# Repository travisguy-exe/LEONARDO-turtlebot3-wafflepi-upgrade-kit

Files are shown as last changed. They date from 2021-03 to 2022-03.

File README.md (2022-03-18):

# LEONARDO - Turtlebot3 (Waffle Pi) Upgrade Kit

**A 3D printable, open-source upgrade kit for the Turtlebot3 Waffle Pi from Robotis.**

 <span xmlns:dct="http://purl.org/dc/terms/" property="dct:title">LEONARDO - Turtlebot3 Waffle Pi Upgrade Kit</span> by <a xmlns:cc="http://creativecommons.org/ns#" href="https://github.com/travisguy-exe/LEONARDO-turtlebot3-wafflepi-upgrade-kit" property="cc:attributionName" rel="cc:attributionURL">Travis Guy</a> is licensed under a <a rel="license" href="http://creativecommons.org/licenses/by-nc-sa/4.0/">Creative Commons Attribution-NonCommercial-ShareAlike 4.0 International License</a>.

## **Kit Overview**

The Leonardo upgrade kit is intended to increase the overall modularity and usability of the Turtlebot3. This is a valuable upgrade for anyone looking to improve the physical user friendliness, durability and modularity of their Turtlebot3 unit. The following list outlines the key features of the Leonardo Kit.



####  **Kit Features:**

- **Enclosures:** Fully 3D printable enclosures for both the Turtlebot3's **Raspberry Pi** and **OpenCR** boards, with solid mounting points.
- **Solid LIDAR Mount:** A 3D printable solid mount for the LDS-01 LIDAR unit.
- **Improved User Experience** Careful consideration was made to relocate both the Raspberry Pi and OpenCR boards to make their ports more easily accessible. This combined with their solid mount points makes connecting peripherals and interfacing with the robot much easier than on the standard model.
- **Improved Modularity:** The Leonardo upgrade kit reimagines the construction of the Turtelbot3's waffle plate frame, allowing it to be segmented and customized without altering the original footprint or waffle plate pattern of the robot.  This feature allows access to the large amounts of free space within the Turtlebot3 frame so you can easily add your own modifications.

## **Repository Overview**

  This repository contains all of the files and instructions necessary to upgrade a standard Turtlebot3 Waffle Pi unit, as well as, the CAD documentation that one would require to add their own features to this upgrade kit. The following list provides detail on each of the sub-folders within this directory and where to locate relevant information within them.

**Repository Folders:**

- **3D Printing Files:** This folder contains all of the necessary **STL** files for printing the upgrade kit's parts.

- **CAD Files:** Contained within this folder are the **Fusion 360** and neutral **.step** solid models for the Leonardo Kit assembly and its sub-assemblies.

------

## **Project Log**

The Leonardo project is still under active development, which means features will be added to this repository as time goes on! Refer back to this log to see what is upcoming and what I have added!

### Work In Progress

- Custom URDF and mesh files of the Leonardo Kit variant for ROS.
- Youtube Assembly/Overview Video

### Completed Work

2021/03/26 - Project Inception

	- CAD Files - Leonardo v80 Master Assemblies
	- Assembly Documentation
	- STL Files/3D Printing Documentation

2022/03/18 - Youtube Assembly Video + CAD Model Update

```
- Assembly Video - Uploaded to Robotis OpenSourceTeam Youtube Channel
- Assembly Instuction - PDF Printable version of assembly documentation added to repository
- CAD Files - Leonardo Master Assembly updated to v83
- STL Files - Updated to Reflect V83 changes:
	 - USB relief added to OpenCR lower enclosure [02 - OpenCR Case (Lower) - (v118)]
	 - Update to RPi upper enclosure chamfer to improve printability [05 - RPi Case (Upper) - (v57)] 
```

------

## Assembly Video

https://youtu.be/VhC4pEQV8hI

## Bill of Materials

The following table outlines the items required to complete the Leonardo upgrade:

| Item/Description | Qty. | |
| :--- | :--: | :---: |
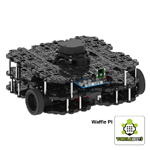
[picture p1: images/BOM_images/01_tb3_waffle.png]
| Turtlebot 3 Waffle Pi Kit |  1 |  |
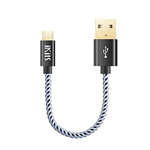
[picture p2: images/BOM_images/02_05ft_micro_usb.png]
| 0.5 ft. Micro USB Cable |  1 |  |
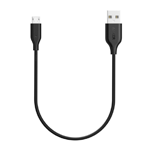
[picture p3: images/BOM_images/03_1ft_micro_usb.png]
| 1 ft. Micro USB Cable |  1 |   |
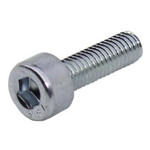
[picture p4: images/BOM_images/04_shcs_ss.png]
| **M3-0.5 x 8mm** - Socket Head Cap Screw |  16  |  |
| **M3-0.5 x 16mm** - Socket Head Cap Screw  |  16  |  |
| **M5-0.8 x 8mm** - Socket Head Cap Screw |  4 |  |
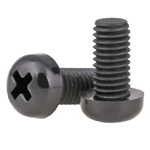
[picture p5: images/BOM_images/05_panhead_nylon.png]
| **M3-0.5 x 6mm** - Pan Head Screw (NYLON)  |  8 |   |
| **M3-0.5 x 12mm** - Pan Head Screw (NYLON) |  2 |   |

# **Assembly Instructions**

	This section outlines the assembly instructions for the Leonardo Upgrade Kit. These instructions assume that you have purchased all items in the **Bill of Materials** section and have 3D printed all relevant upgrade parts in accordance with the instructions laid out in the readme of the **3D Printing Files** folder.

------

### Step 1: TB3 First Layer Assembly

------

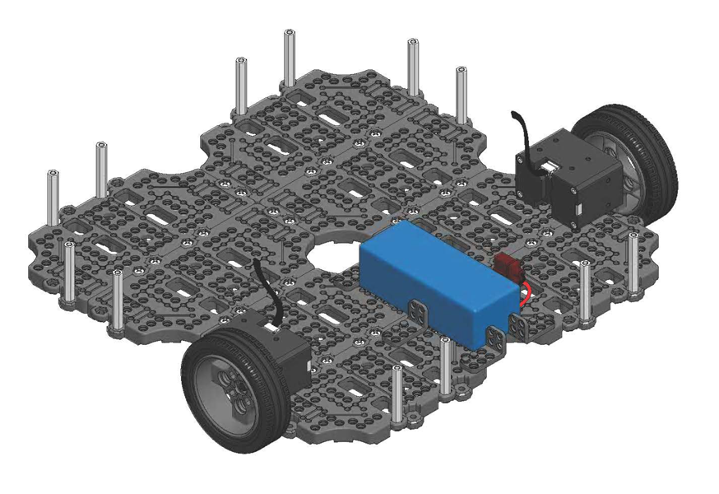
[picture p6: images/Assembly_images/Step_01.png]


The Leonardo upgrade kit uses the **"First Layer Assembly"** from the standard Turtlebot3 Waffle Pi. Specific instructions for assembling the **"First Layer Assembly"** can be found on **Pages 16-20** of the Robotis Turtlebot3 Waffle Pi Assembly Manual. Once assembled, the First Layer Assembly can be set aside until **Step 4**

**Robotis Assembly Manual (Direct Download):** https://www.robotis.com/service/download.php?no=750

------

### Step 2: TB3 Second Layer Assembly

------

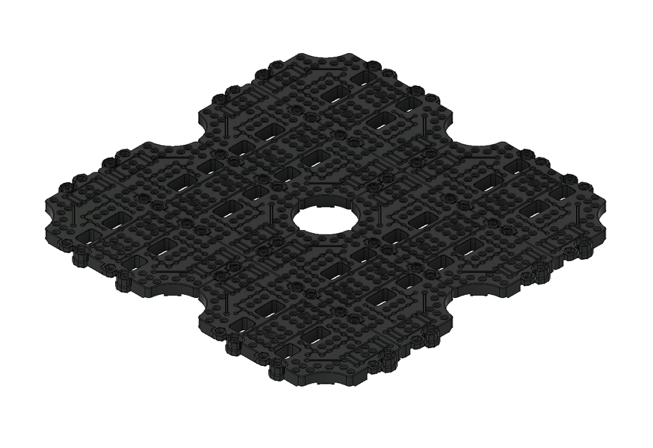
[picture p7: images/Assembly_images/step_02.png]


The Leonardo upgrade kit also uses the **"Second Layer Assembly"** from the standard Turtlebot3 Waffle Pi. Assembly instructions for the **"Second Layer Assembly"** can be found on **Pages 12-13** of the Robotis Turtlebot3 Waffle Pi Assembly Manual.  A fully assembled Second Layer is required before proceeding to **Step 3.**

------

### Step 3: Second Layer Drill & Tap Locations (Enclosure Mounting)

------

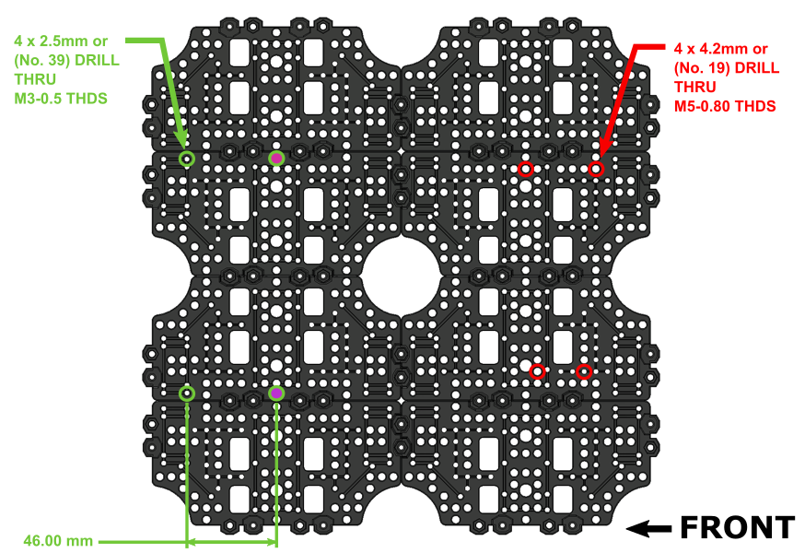
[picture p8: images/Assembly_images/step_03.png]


In order to attach the Raspberry Pi and OpenCR board enclosures, **6 pre-existing** holes must be modified and **2 new** holes must be added on the Second Layer Assembly.  

The **Step 3** image above indicates the relevant hole locations as well as their respective drill and tap sizes. The hole locations marked with **PINK** indicate where a new hole must be drilled. The location distances for the new holes are denoted on the image above, however, if one wishes to avoid measuring, the 3D printed lower case of the OpenCR board enclosure can be used as a template to transfer the hole locations to the waffle plate before drilling.

**NOTE:** Orientation of the second layer assembly matters from this step onwards. Be sure to follow the orientation indicators for each subsequent step.

------

### Step 4: Second/Third Layer Standoff Installation

------

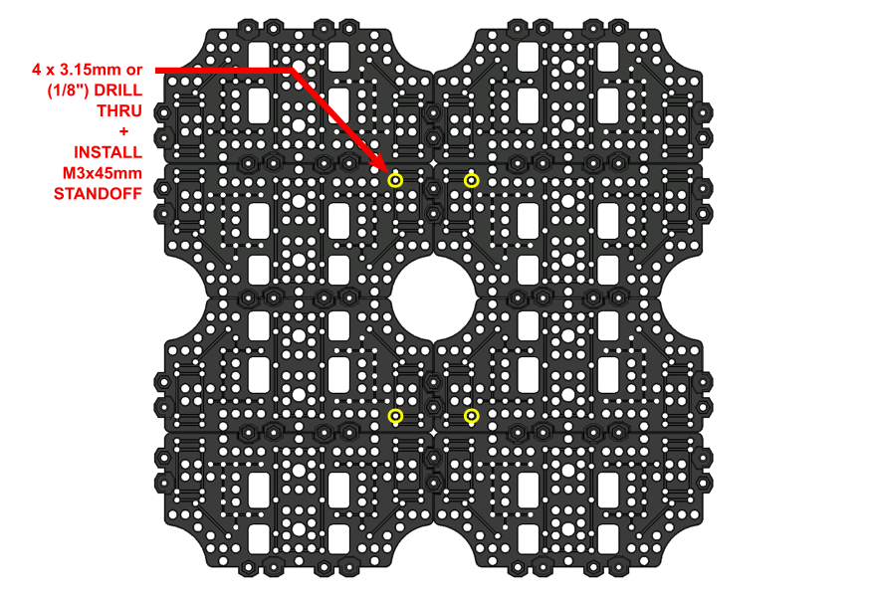
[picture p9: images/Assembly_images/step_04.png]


The third layer of the Leonardo upgrade kit is supported by **4 - M3x45mm Standoffs** attached to the second layer assembly. These standoffs are re-purposed hardware from the standard Turtlebot3 kit and can be obtained from such. **4 - M3x16mm** fasteners will be required to attach the standoffs.

The Step 4 image above indicates the correct installation location of each standoff, before installation the indicated holes must be  drilled out for an M3 free fit (3.15mm or 1/8" Drill).

**NOTE:** Ensure mounting screws for the standoffs are tightly secured and in the correct positions before proceeding. Once the second layer assembly is attached to the first, you will loose convenient access to the screw heads for these standoffs.

------

### Step 5: Second Layer Attachment + Cable Routing

------

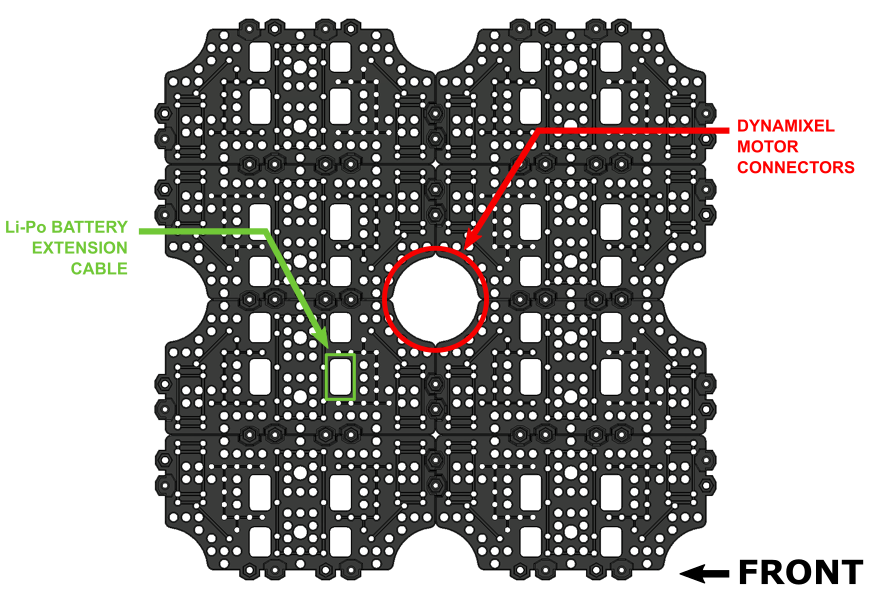
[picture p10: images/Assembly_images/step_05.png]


At this stage the **Second Layer Assembly** created in **Step 2** can be attached to the **First Layer Assembly** created in **Step 1**. However, before attachment, the **Dynamixel Motor Cables** and the **Li-Po Battery Extension Cable** from the first layer must be correctly routed through the bottom of the Second Layer Assembly. The **Step 4** image above shows the respective routing locations for the cables. 

A total of **12 - M3x8mm** screws will be required to attach the second layer to the first. Socket head cap screws can be used if you wish, or you can repurpose the Philips head hardware of the same size from the original Turtlebot3 kit. 

------

### Step 6: OpenCR + Raspberry Pi Installation 

------

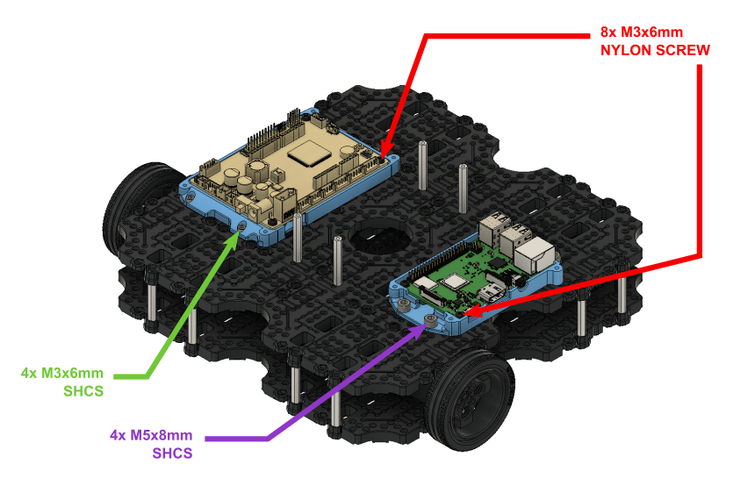
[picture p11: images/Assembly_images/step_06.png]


The **OpenCR** board and **Raspberry Pi**  can now be installed into their respective enclosure halves using **8 - M3x6mm Nylon Screws**. Once installed the enclosures can be attached to the **Second Layer Assembly** using the drilled and tapped holes created in **Step 2** of these instructions. The **Step 5** image above shows the required mounting hardware and respective installation locations.

**NOTE:** The mounting holes on the Raspberry Pi board may need to be enlarged for the M3 Nylon Screws if you have a brand new board. A 3.15mm or (1/8") drill bit will suffice for this process.

------

### Step 7: OpenCR Board Connections + Bluetooth Module Installation (BT-410)

------

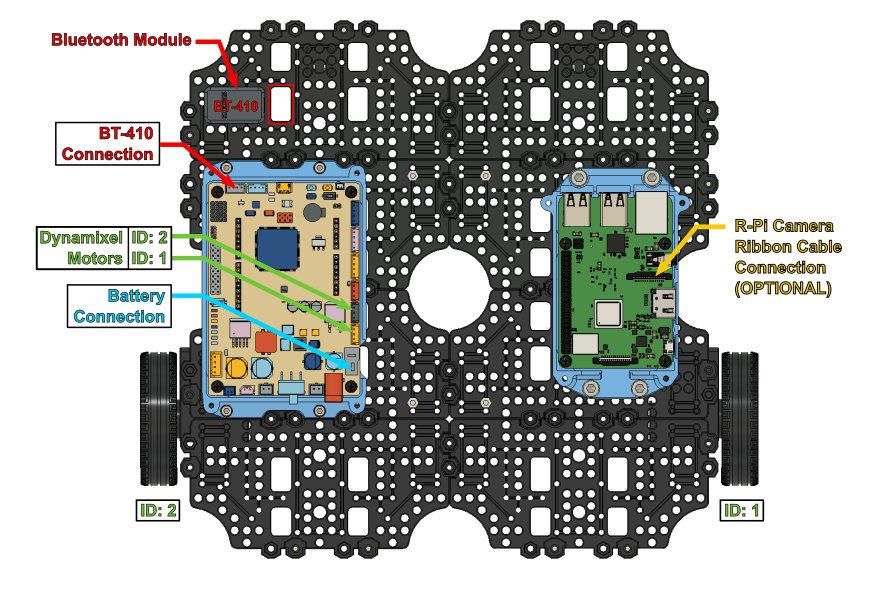
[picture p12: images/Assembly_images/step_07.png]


- [ ] Attach the **Dynamixel Motor** cables and **Li-Po Battery Extension** cable that were routed during **Step 5** to the OpenCR board. The connection points are indicated by the **Green** and **Blue** arrowed text in the image above. 

  **NOTE:** Ensure correct connection of the Dynamixel motors by following the motor ID legend in the **GREEN** arrowed text. The motor IDs are indicated below each wheel for quick reference.

- [ ] Once the motor and battery connections are made, attach the **BT-410 Bluetooth Module** to the second layer assembly. The **RED** arrowed text above indicates its installation location as well as connection point on the OpenCR board.

  **NOTE:** The opening highlighted by the **RED** rectangle can be used to neatly tuck away the excess cable from the Bluetooth module.

- [ ] **OPTIONAL:** If you wish to use the standard Raspberry Pi camera that comes with the Turtlebot3 kit, now is the easiest time to connect the camera's ribbon cable. The **ORANGE** arrowed text above indicates its connection point.

  **NOTE:** It is easy to connect the camera cable backwards, ensure that the camera ribbon cable is connected in the correct orientation (Contacts on the ribbon cable facing the contacts on the port.)

------

### Step 8: Enclosure Assembly + Raspberry Pi Power Connection

------

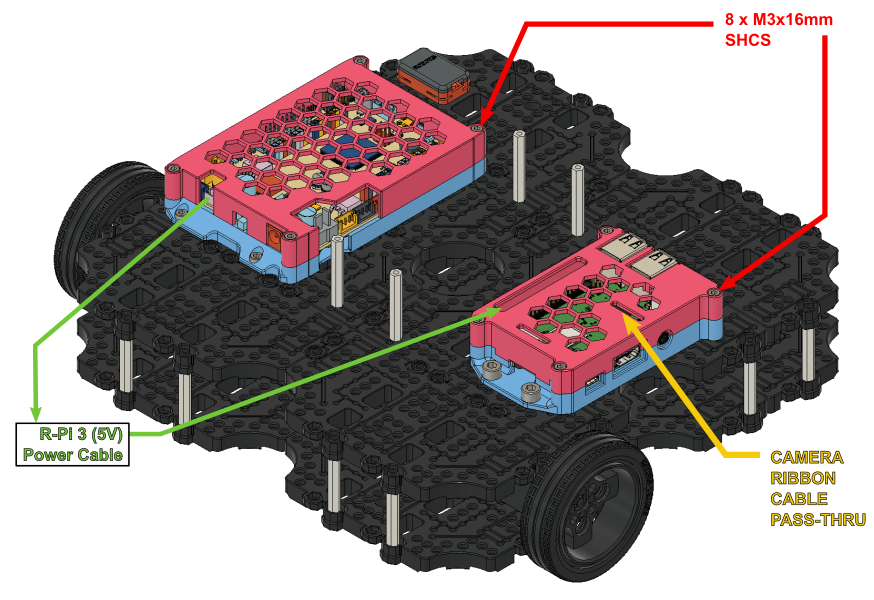
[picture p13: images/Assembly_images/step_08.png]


- [ ] The top halves of the enclosure cases can now be attached to the assembly. As indicated in the assembly image above, a total of **8 - M3x16mm** fasteners will be required. If you are using a R-Pi camera, be sure to route the ribbon cable through the pass through opening indicated above by the **YELLOW** arrowed text.

- [ ] Once the enclosure cases are securely installed the 5V power connection between the OpenCR board and the Raspberry Pi board can be made. This is done using the **Raspberry Pi 3 Power Cable** from the standard Turtlebot3 kit.  The **GREEN** arrowed text in the image above indicates the connection points.

  **NOTE:** When connecting the power cable to the Raspberry Pi it is important to connect to the correct GPIO pins. Ensure that the **Positive** lead connects to **Pin 4** and the **Negative** lead connects to **Pin 6**. 

  (Refer to **Page 23** of the Turtlebot3 Waffle Pi Assembly Manual for connection information.)

------

### Step 9:  Third Layer Assembly + Tap & Drill Instructions

------

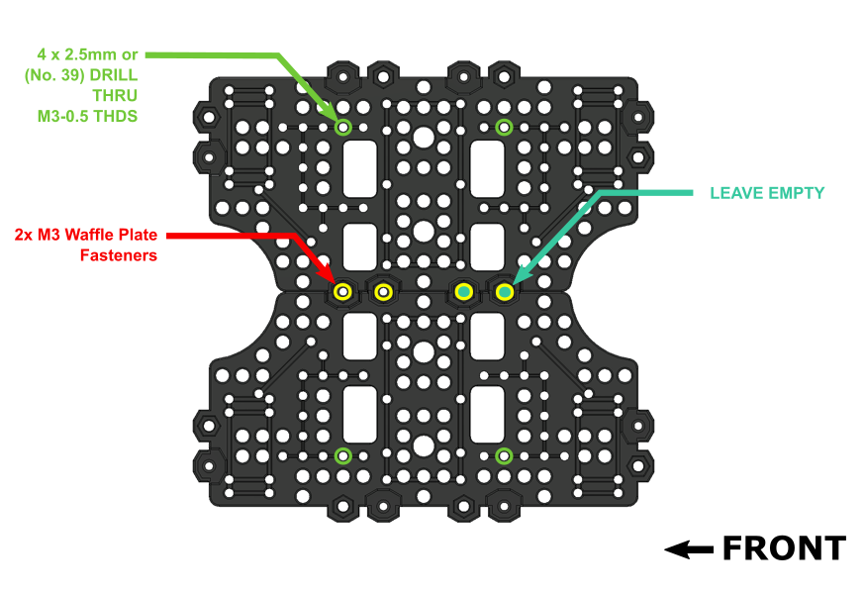
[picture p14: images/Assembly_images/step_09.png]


The third layer of the Leonardo upgrade requires only two waffle plates from the standard Turtlebot3 kit. The **Step 9** image above shows the manner in which the plates are connected and, indicates the fastener installation locations.

**NOTE:** It is important to leave the two M3 fastener locations indicated in the image above empty. These locations are used for attaching the USB2LDS driver board in the next step.

Once the waffle plates are assembled, and, before proceeding to the next step, a total of **4** pre-existing holes on the assembly must be modified. The **GREEN**  arrowed text in the **Step 9** image above indicates the relevant holes, as well, their respective drill and tap information.

------

### Step 10:  USB2LDS Module Installation

------

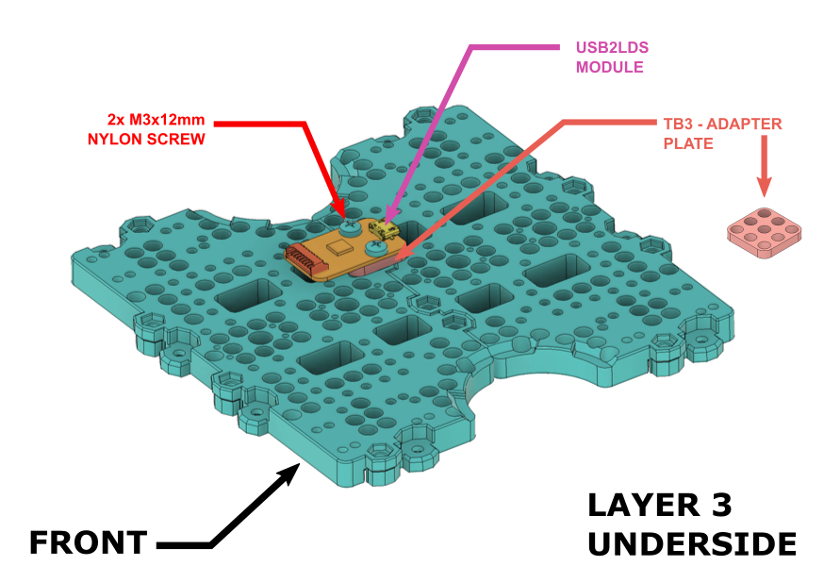
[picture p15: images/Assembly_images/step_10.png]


The USB2LDS module from the standard Turtlebot3 kit can now be installed on the underside of the the third layer assembly.  The module requires **2 - M3x12mm Nylon screws** that are fastened through the waffle plates in the fastener locations left empty in **Step 9**. As indicated in the image above the assembly also requires the **"Adapter Plate"** component from the standard Turtlebot3 kit, this component acts as a spacer for the module.

**NOTE:** The Nylon screws will protrude through the topside of the waffle plates. Use a pair of **flush-cut pliers** to trim the excess after the module has been tightly secured.

------

### Step 11:  LIDAR Mounting Bracket Installation

------

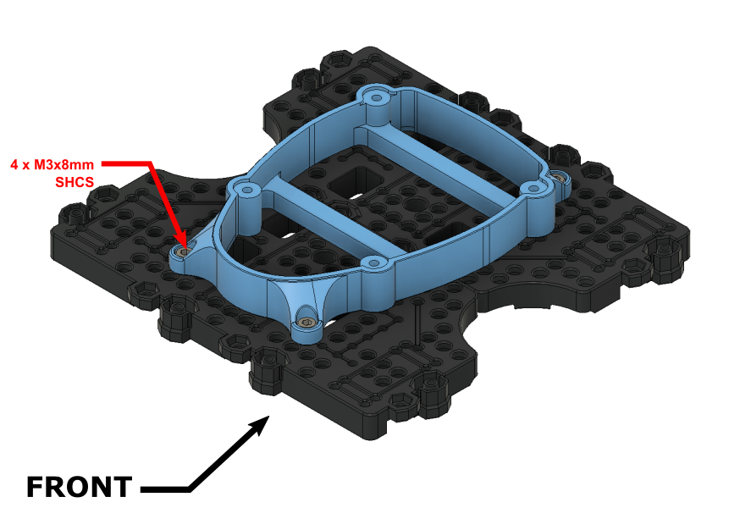
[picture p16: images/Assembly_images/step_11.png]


Turn the Layer 3 assembly back over and attach the LIDAR mount bracket to the top side using **4 - M3x8mm Socket Screws**.  The LIDAR bracket's mounting position corresponds with the 4 drilled and tapped holes made previously in **Step 9**.

------

### Step 12:  LIDAR Module Installation (LDS-01)

------

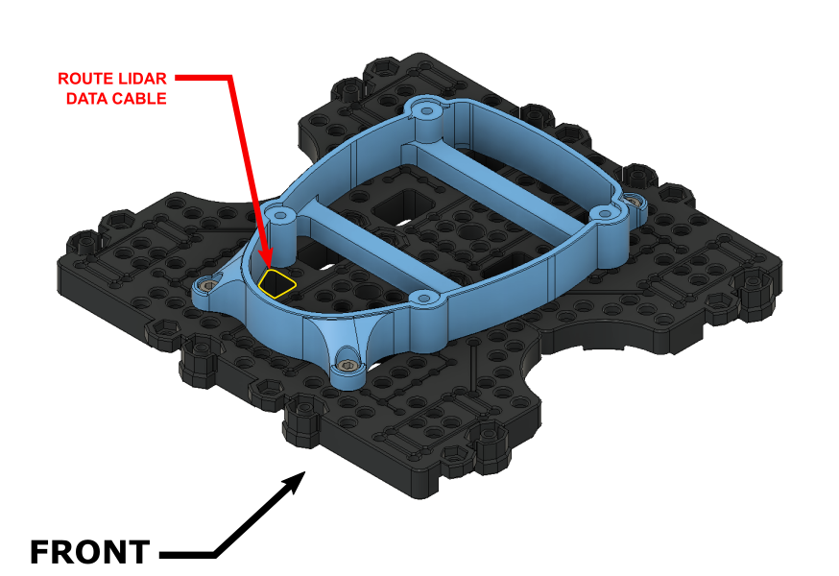
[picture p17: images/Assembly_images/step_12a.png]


------

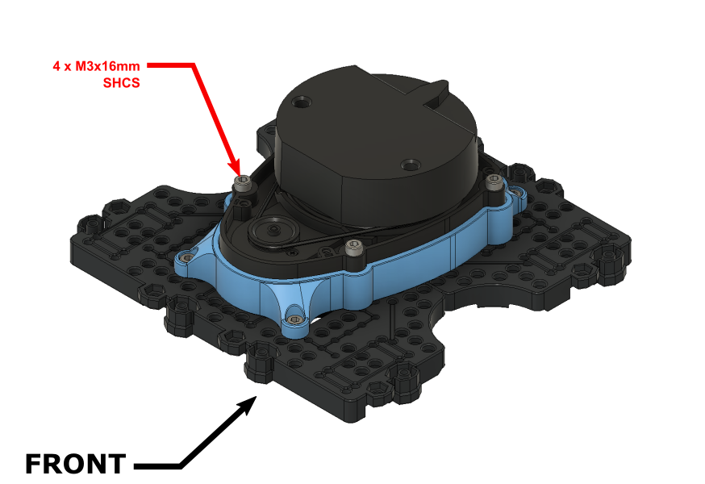
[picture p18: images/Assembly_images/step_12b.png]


See the **NOTE** below before proceeding. Attach the LDS-01 LIDAR unit from the standard Turltbot3 kit to the mounting bracket using **4 - M3x16mm Socket Screws**. Be sure to route the unit's data cable though the opening highlighted in **YELLOW** in the image above before fastening. Once fastened make sure to attach the LDS-01's data cable to the USB2LDS module on the underside of the layer.

**NOTE:** The LIDAR unit's mounting holes will have to be modified to accept M3 sized fasteners. Drill out the 4 indicated mounting holes using a 3.15mm or (1/8") drill bit.

------

### Step 13:  Third Layer Attachment

------

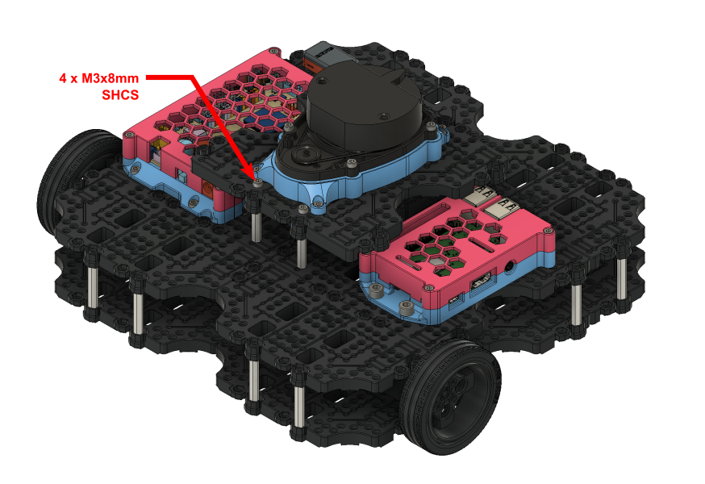
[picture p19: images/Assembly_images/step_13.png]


Attach the third layer assembly to the standoffs that were previously installed on the second layer assembly during **Step 4**. This will require **4 - M3x8mm Socket Screws**.

------

### Step 14:  Pi Camera Module Installation (Optional)

------

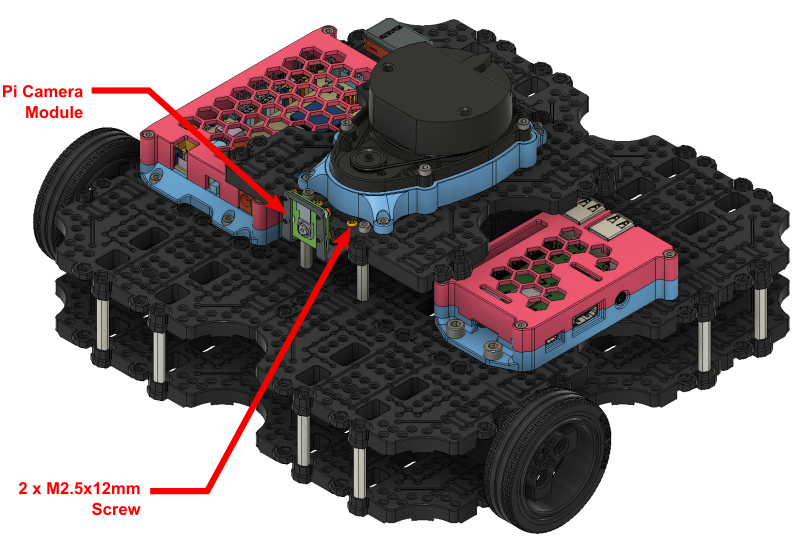
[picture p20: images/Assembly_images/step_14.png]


If you plan on using the standard Pi Camera module that comes with the Turltbot3 kit, it can now be easily attached to the **Third Layer Assembly ** using the standard M2.5x12mm mounting hardware that comes with it. 

**NOTE:** See page 30 of the Robotis Turtlebot3 Waffle Pi Assembly Manual for detailed instructions on assembling the Pi Camera module.

------

### Step 15: USB Connections and Cable Routing

------

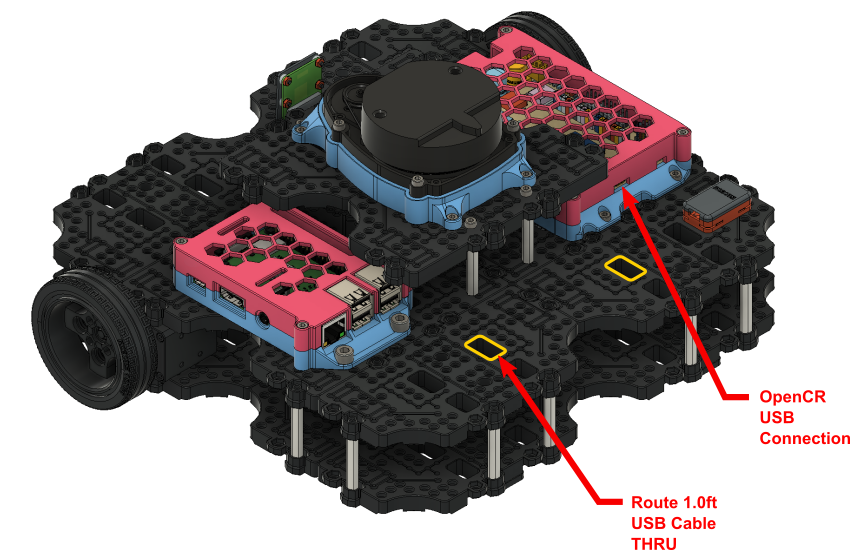
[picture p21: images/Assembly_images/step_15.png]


The final steps are to make the USB connections to both the USB2LDS module and the OpenCR board from the Raspberry Pi unit.

- [ ] Connect the 0.5ft micro USB cable from the Raspberry Pi unit to the USB2LDS module beneath the third layer assembly
- [ ] Connect the 1.0ft micro USB cable from the Raspberry Pi unit to the OpenCR board.

**NOTE:** The 1.0ft micro USB cable should be routed through the holes highlighted in **YELLOW** on the way towards the OpenCR board, this will keep the cable routing tidy and out of the way during use.

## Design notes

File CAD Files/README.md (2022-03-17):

# **LEONARDO - CAD FILES - (v83)**

This folder contains the master assembly file for the LEONARDO mod kit, it is available in 2 different formats (**.f3z** & **.step**). The image below depicts the contents of the assembly files.

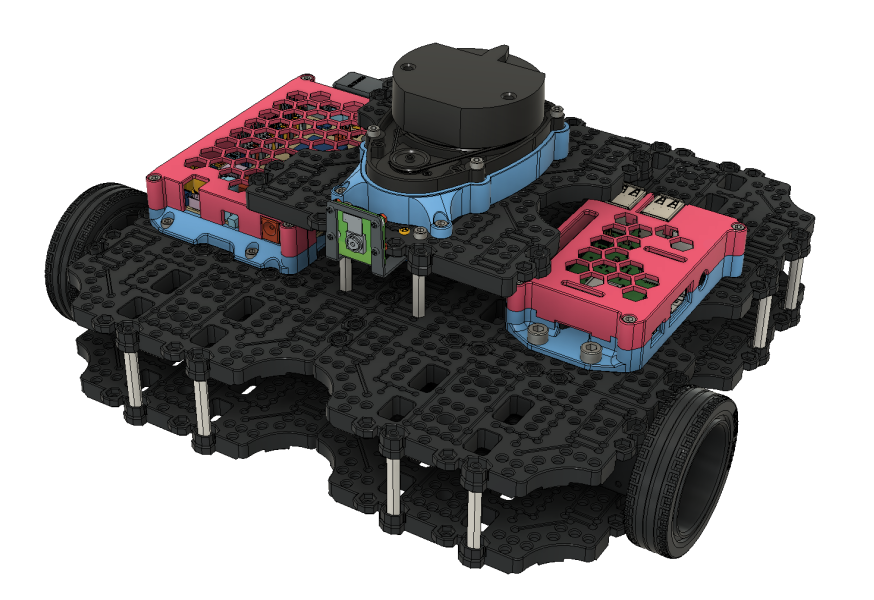
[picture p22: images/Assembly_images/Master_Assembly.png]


The LEONARDO mod kit was developed in **Fusion 360**, if this is your native CAD program I recommend downloading the **.f3z** format of the master assembly. This will provide you with the master assembly and all of the individual linked sub-assemblies. The .f3z file also contains captured design history of each part, for ease of personal modification. 

If you are **not** a **Fusion 360** user, you can still download the neutral format of the master assembly (**.step**). This variant, however, exists as single standalone assembly and does not contain any of the captured design history.

**Special License Considerations & Credits:**

[1] - The sub-assembly "RPi Case - Assembly" was based upon the work of Thingiverse user "[0110-M-P](https://www.thingiverse.com/0110-M-P)" and is licensed as follows:

 <span xmlns:dct="http://purl.org/dc/terms/" property="dct:title">RPi Case - Assembly</span> by <a xmlns:cc="http://creativecommons.org/ns#" href="https://github.com/travisguy-exe/LEONARDO-turtlebot3-wafflepi-upgrade-kit" property="cc:attributionName" rel="cc:attributionURL">Travis Guy</a> is licensed under a <a rel="license" href="http://creativecommons.org/licenses/by-sa/4.0/">Creative Commons Attribution-ShareAlike 4.0 International License</a>. Based on a work at <a xmlns:dct="http://purl.org/dc/terms/" href="https://www.thingiverse.com/thing:922740" rel="dct:source">https://www.thingiverse.com/thing:922740</a>.

[2] - The standard CAD assets of the Turtlebot3 Waffle Pi unit were obtained from Robotis, and can be found at the following link:

https://cad.onshape.com/documents/179d4ba2a1f9231f93cae6e2/w/71e9066aee42d5039f880e2f/e/3cb7d487c93655e7067a3d5f

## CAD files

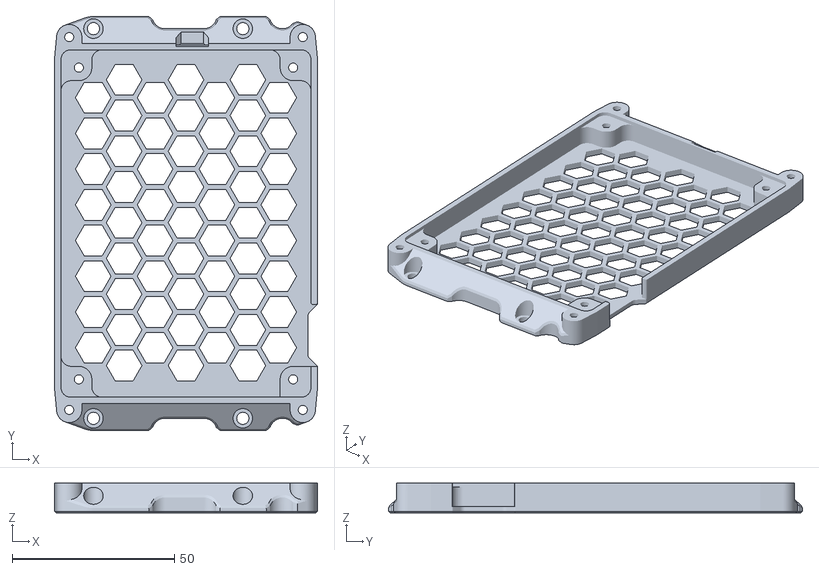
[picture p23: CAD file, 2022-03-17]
3D Printing Files/02 - OpenCR Case (Lower) - (v118).stl
81.0 x 127.5 x 9.20

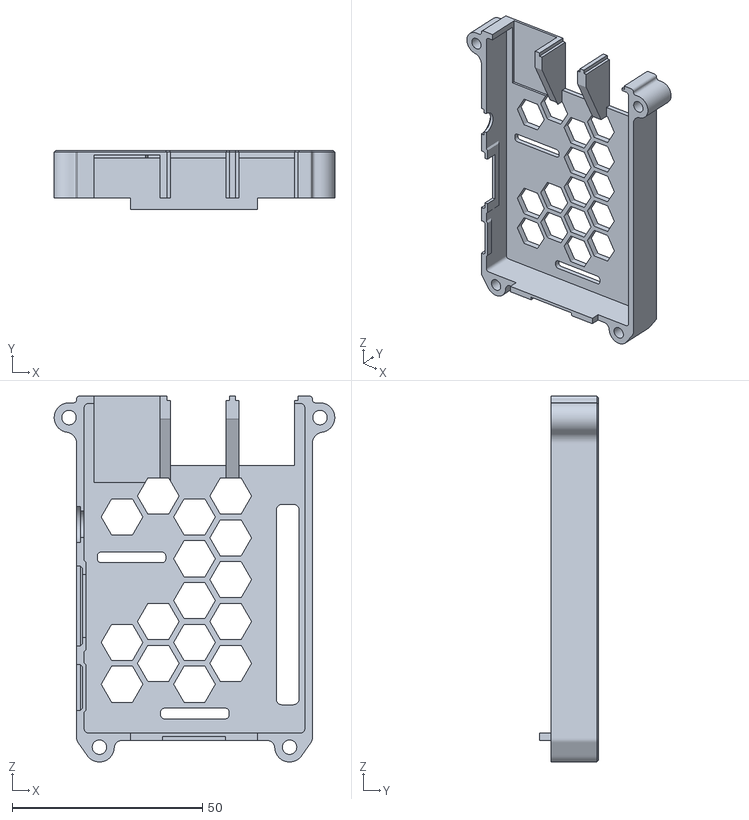
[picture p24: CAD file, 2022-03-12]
3D Printing Files/05 - RPi Case (Upper) - (v57).stl
73.8 x 15.5 x 96.2

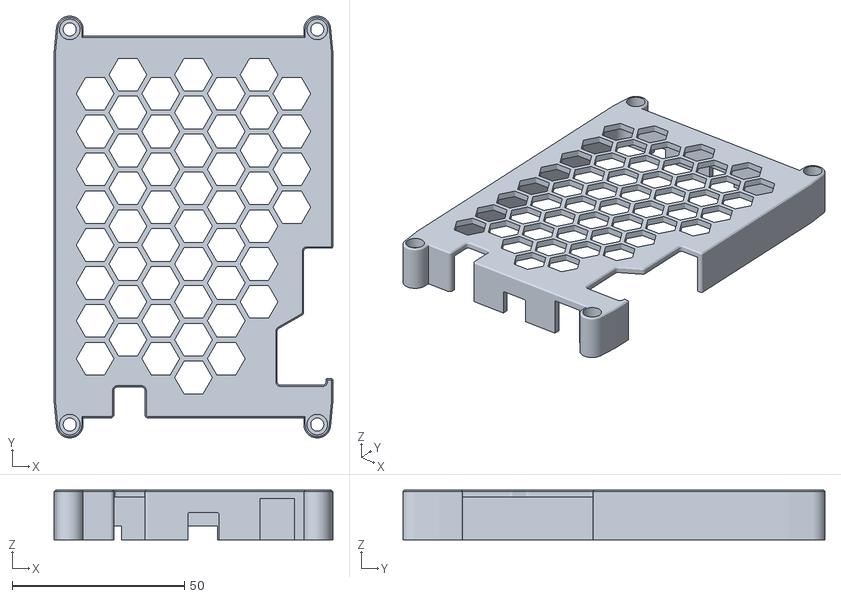
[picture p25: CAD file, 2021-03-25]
3D Printing Files/03 - OpenCR Case (Upper) - (v114).stl
81.0 x 122.6 x 14.5

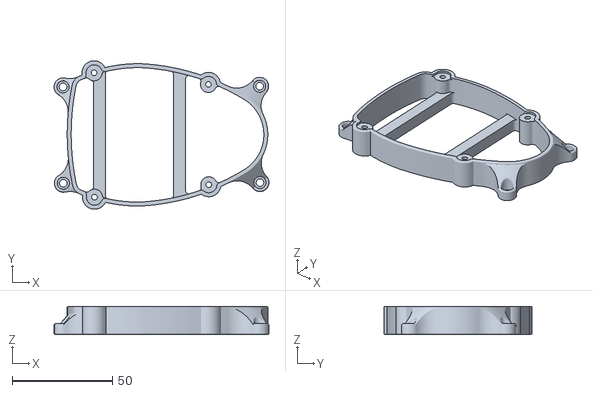
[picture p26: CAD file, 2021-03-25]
3D Printing Files/01 - LIDAR Mounting Bracket - (v25).stl
107.2 x 74.0 x 14.0

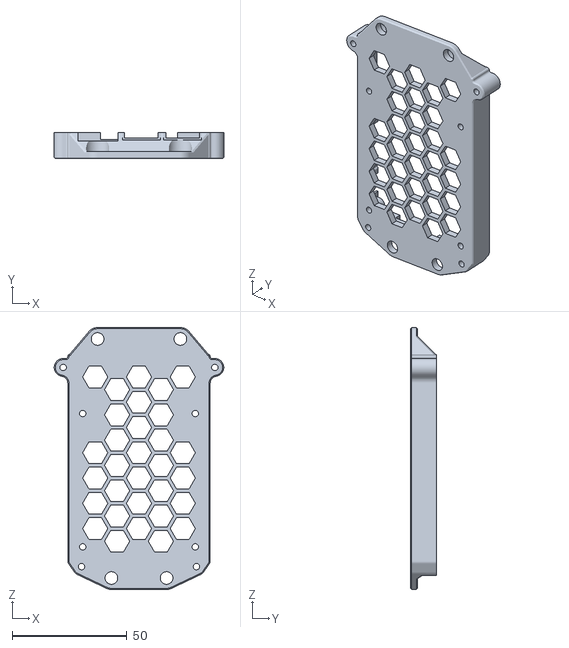
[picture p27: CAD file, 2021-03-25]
3D Printing Files/04 - RPi Case (Lower) - (v55).stl
73.8 x 11.3 x 114.0

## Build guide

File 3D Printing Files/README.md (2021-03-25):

## 3D Printing/Post Processing Instructions

The LEONARDO upgrade kit requires **1** print of each part contained within this sub folder. The parts have been designed to be easily printable on any FDM type printer. 

Once printed, several holes on Parts No. **01**, **02**, and **04** require **tapping**, an **M3-0.5** tap is required for this process. The **RED** circles in the image below indicate the relevant holes that require tapping on each part.

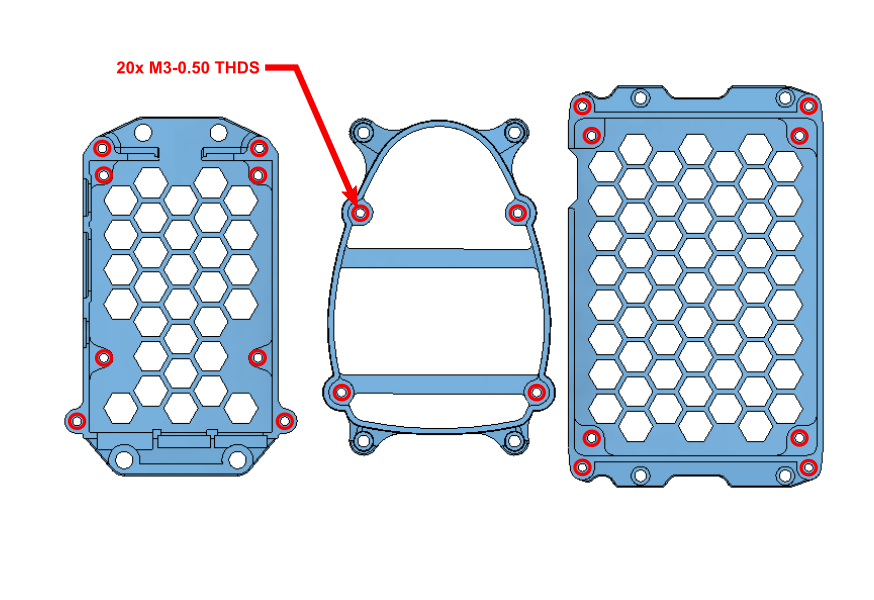
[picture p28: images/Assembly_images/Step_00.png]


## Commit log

2021-03-24 Create LEONARDO - Master Assembly - (v80).f3z
2021-03-24 Create LEONARDO - Master Assembly - (v80).step
2021-03-25 STL File Upload
    [01 - LIDAR Mounting Bracket - (v25).stl, 02 - OpenCR Case (Lower) - (v114).stl, 03 - OpenCR Case (Upper) - (v114).stl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]
2021-03-25 3D Printing Instructions Upload
2021-03-25 CAD File README Update
2022-03-12 Assembly Image Update
    Cleaned up missing backgrounds on various assembly images.
2022-03-12 Master Assembly V82 Update
    Small Fix Update:
    - Added USB relief on OpenCR lower enclosure half
    - Increased diameter of outer fastener holes on OpenCR lower enclosure half. (2.80mm) - easier to tap after printing
    - Reduced perimeter chamfer causing print issues on Upper RPi enclosure half.
    - Updated layer 2 fasteners to use 45mm standoffs between layers 2 and 3.
2022-03-12 STL File Update
    Small part fix update in accordance with changes made in V82 update of the master assembly.
    [02 - OpenCR Case (Lower) - (v114).stl, 02 - OpenCR Case (Lower) - (v117).stl, 04 - RPi Case (Upper) - (v55).stl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]
2022-03-12 Create Printable Assembly Instructions - Leonardo Upgrade Kit (V82).pdf
2022-03-17 OpenCR Lower Enclosure v118 Update
    Increased USB relief pocket depth
    [02 - OpenCR Case (Lower) - (v117).stl, 02 - OpenCR Case (Lower) - (v118).stl]
2022-03-17 Master Assembly v83 Update
    Assembly updated to reflect changes with v118 of OpenCR Lower Enclosure Half
2022-03-18 Update README.md
    YouTube Assembly Video link added
